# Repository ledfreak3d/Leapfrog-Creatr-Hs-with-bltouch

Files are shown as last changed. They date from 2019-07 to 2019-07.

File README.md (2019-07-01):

Latest Marlin firmware for Leapfrog Creatr Hs based on Marlin 2.0.0 Beta

100% Compatible with the original mainboard

### WARNING ! 	
These releases seems to break communication with the display (Olimex A20). 

( Probably because by defaut Creatr HS use Checksumed Protocol ? )
### WARNING ! 	

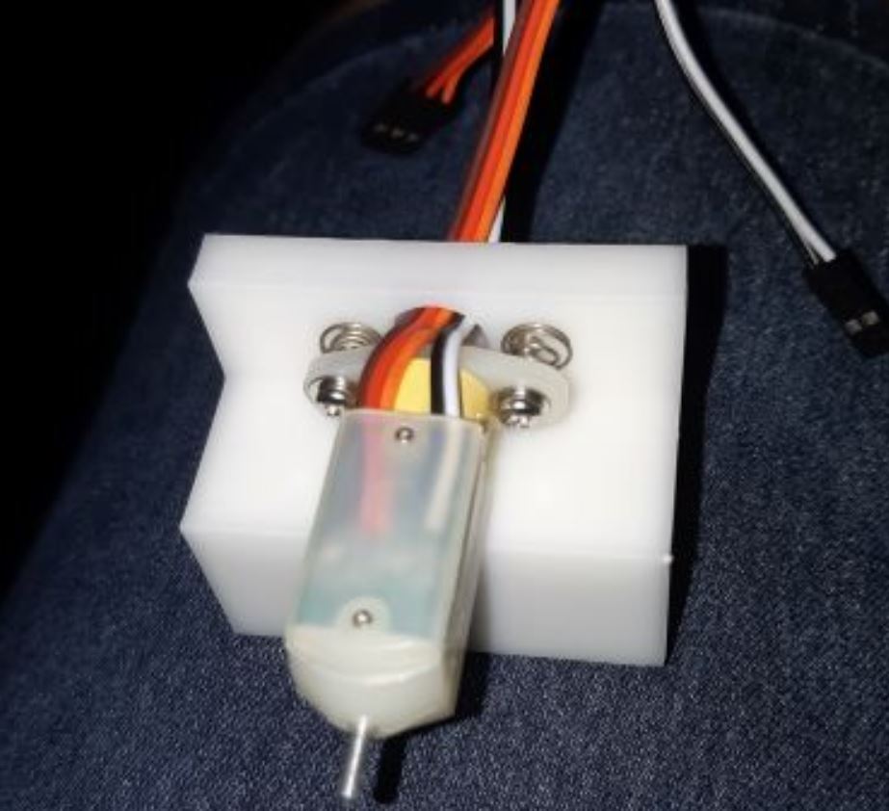
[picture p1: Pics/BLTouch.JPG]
BLTouch img


## Marlin BLTouch (same Standard settings)
- Add BLTouch
- Connect Z (Black/White) on Zmin connector
- Connect SERVO0_PIN on 52 (SCK) (physical pin 20 of ATMega2560) (see pictures)
 
Once installed, use this sequence to determine if the BLTouch is setup properly :

    Connect BLTouch, power up controller and upload the firmware
    
    LED will be ON if a servo signal is present.
    
    M119		; should return OPEN. If not check that the BLTouch is enabled in the configuration. If enabled then check wiring and Check that the correct pin is being used. Also check that Z_MIN_ENDSTOP_INVERTING and Z_MIN_PROBE_ENDSTOP_INVERTING are both set to "false".
    
    M280 P0 S10 	; should deploy the probe and the orange LED will be OFF.
    
    M119 		; should return OPEN
    
    M280 P0 S90 	; should stow the probe and the orange LED will be ON
    
    M280 P0 S60 	; puts it into the M119 test mode.
    		; The probe should remain stowed and the blue LED should be OFF. If it's ON then the unit needs to be adjusted.
    
    M119 		; should return TRIGGERED
    
    M280 P0 S160 	; returns it to normal operation
    
    M119 		; should return OPEN.
    
  After this Z offset needs to be callibrated !!!
  A good video guide to use for this is  https://www.youtube.com/watch?v=y_1Kg45APko&list=FLQG47LoNpPy0yjQeLG1prTA&index=2&t=0s
  
  Also make sure you setup your gcode correctly so auto bed leveling is done on every print
  See Simplify3d profiles for more info

Future update : 
 
-Upgrade to 32bit controller board

-Replacing the Olimex display for a touch display

-Upgrade Olimex to Octoprint

Cudo's to Vil Coyote for creating the mount that holds the bltouch
 
Forked from : https://github.com/CoyoteProd/Leapfrog-Creatr-HS/tree/master/Marlin%20BLTouch

Original Firmware : https://github.com/Leapfrog3DPrinters/CreatrHS_Firmware_2.5

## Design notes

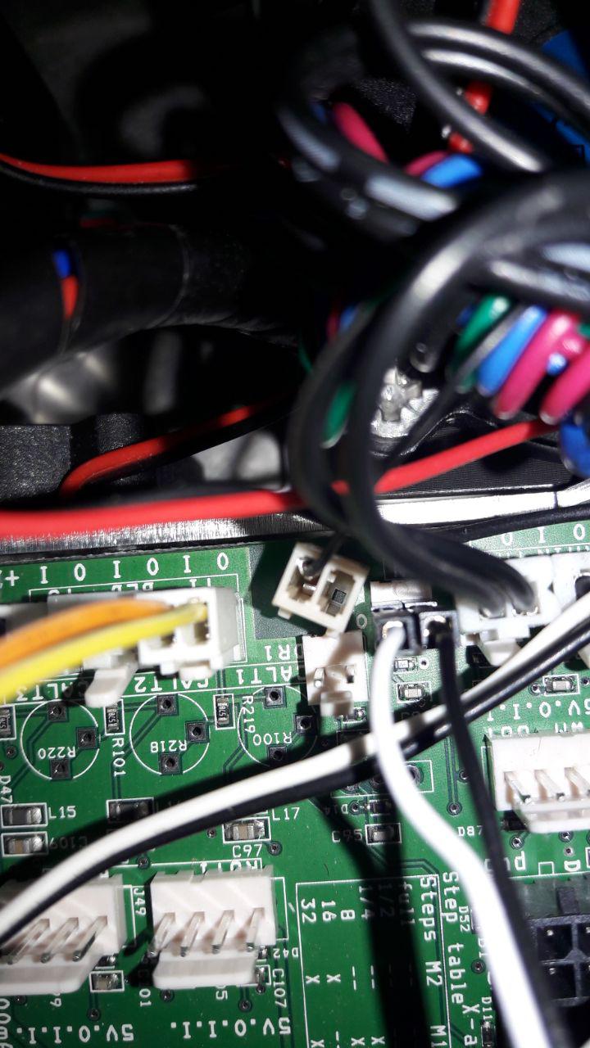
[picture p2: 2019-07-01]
Pics/Z-limit.jpg

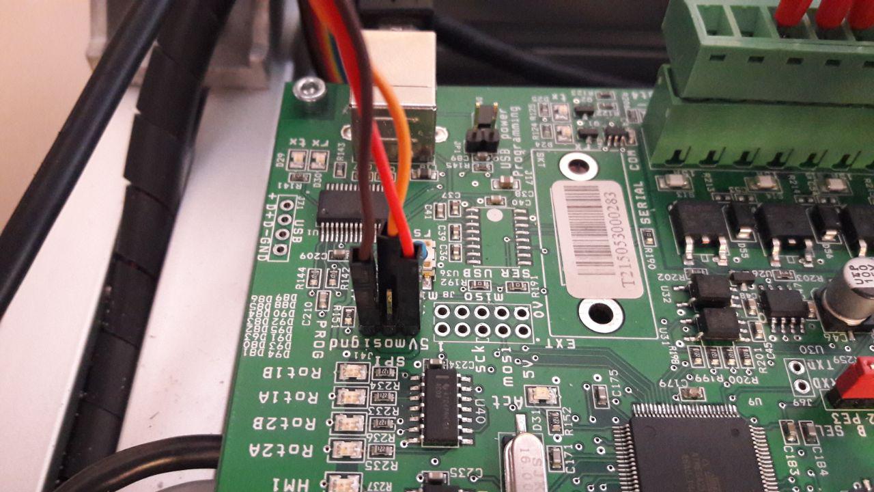
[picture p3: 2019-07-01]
Pics/Servo.jpg

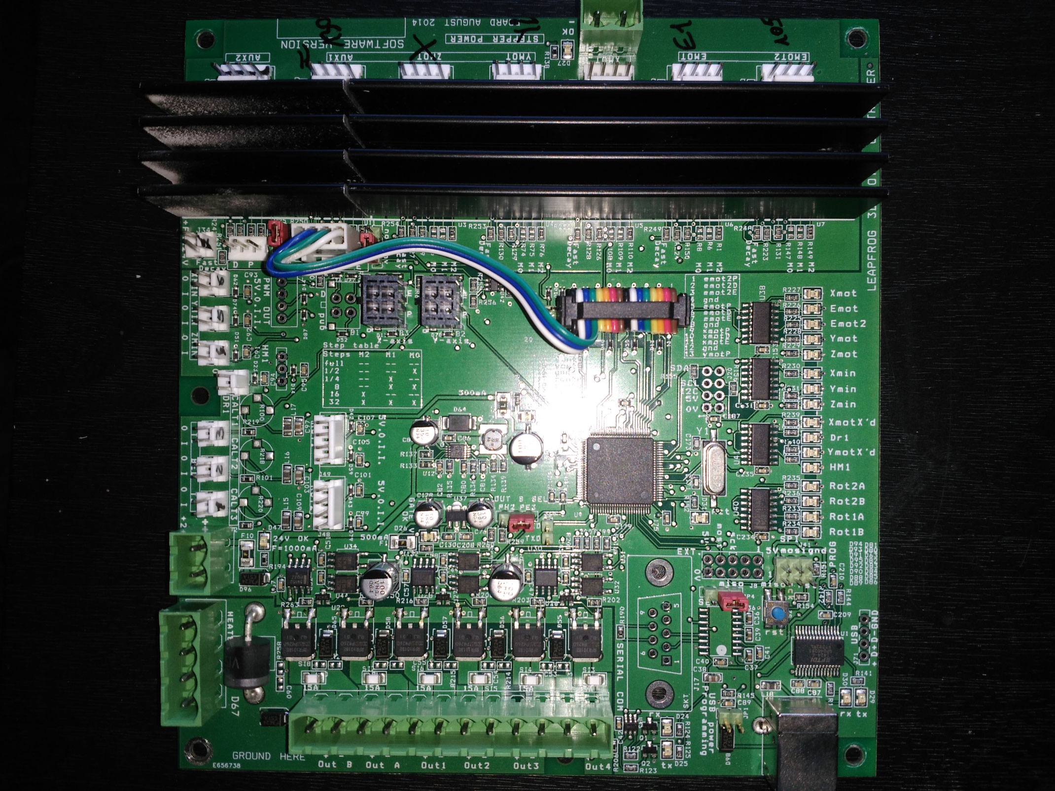
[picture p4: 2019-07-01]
Pics/image.jpg

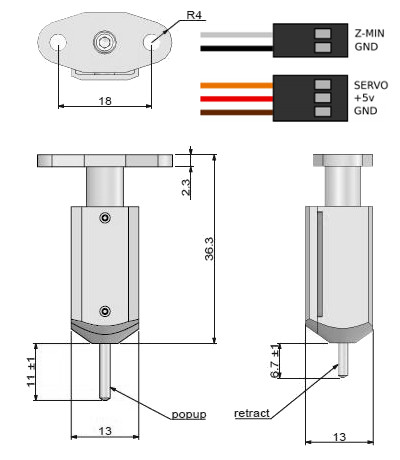
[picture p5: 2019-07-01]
Pics/BLTouch1.jpg

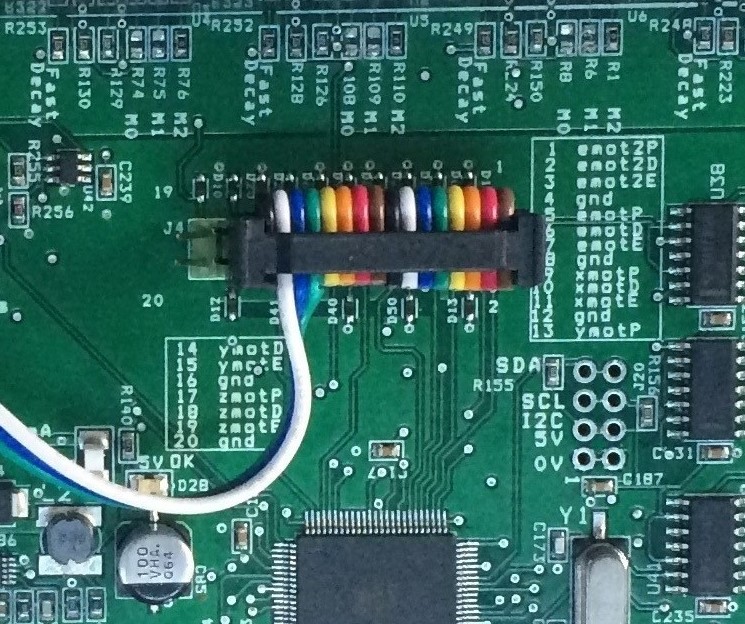
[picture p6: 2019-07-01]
Pics/oU3_eYAFjFmzLhcsRAwmdgnGUxJsZOXy3g (2).jpg

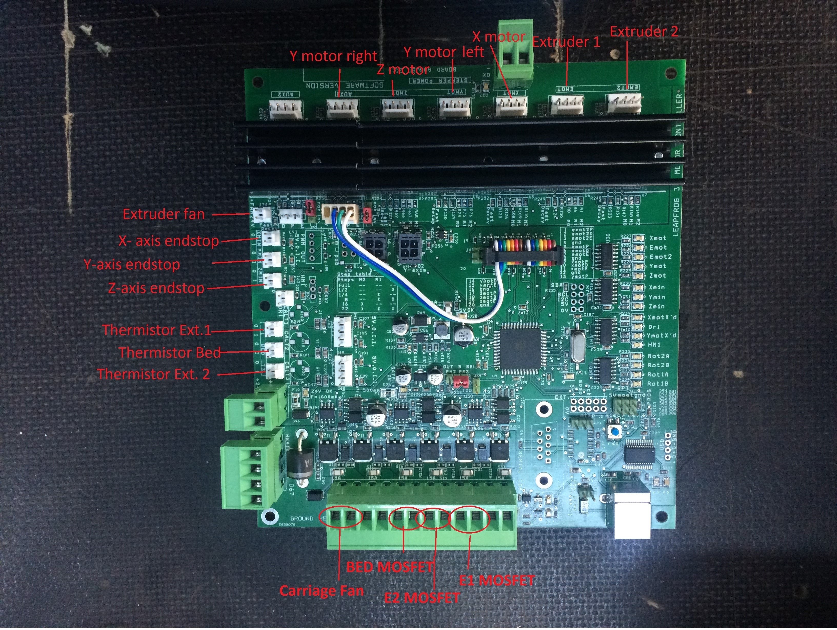
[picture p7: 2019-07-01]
Pics/oU3_eYAFjFmzLhcsRAwmdgnGUxJsZOXy3g.jpg

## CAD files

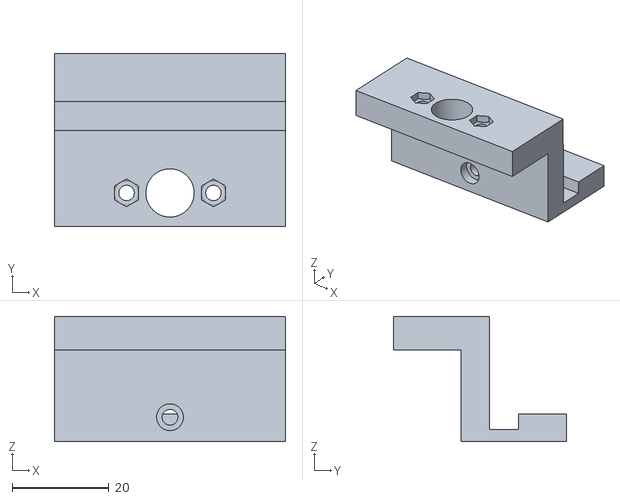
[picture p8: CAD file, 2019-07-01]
Support/support BLTouch.stl
47.9 x 35.9 x 26.0

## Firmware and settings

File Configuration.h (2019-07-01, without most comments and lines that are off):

#pragma once
#define CONFIGURATION_H_VERSION 020000
#define STRING_CONFIG_H_AUTHOR "(none, default config)" // Who made the changes.
#define SHOW_BOOTSCREEN
#define STRING_SPLASH_LINE1 SHORT_BUILD_VERSION // will be shown during bootup in line 1
#define STRING_SPLASH_LINE2 WEBSITE_URL         // will be shown during bootup in line 2
#define SERIAL_PORT 0
#define BAUDRATE 250000
  #define MOTHERBOARD BOARD_LEAPFROG
#define EXTRUDERS 2
#define DEFAULT_NOMINAL_FILAMENT_DIA 1.75
#define POWER_SUPPLY 0
#define TEMP_SENSOR_0 1
#define TEMP_SENSOR_1 1
#define TEMP_SENSOR_2 0
#define TEMP_SENSOR_3 0
#define TEMP_SENSOR_4 0
#define TEMP_SENSOR_5 0
#define TEMP_SENSOR_BED 1
#define TEMP_SENSOR_CHAMBER 0
#define DUMMY_THERMISTOR_998_VALUE 25
#define DUMMY_THERMISTOR_999_VALUE 100
#define MAX_REDUNDANT_TEMP_SENSOR_DIFF 10
#define TEMP_RESIDENCY_TIME     10  // (seconds) Time to wait for hotend to "settle" in M109
#define TEMP_WINDOW              1  // (°C) Temperature proximity for the "temperature reached" timer
#define TEMP_HYSTERESIS          3  // (°C) Temperature proximity considered "close enough" to the target
#define TEMP_BED_RESIDENCY_TIME 10  // (seconds) Time to wait for bed to "settle" in M190
#define TEMP_BED_WINDOW          1  // (°C) Temperature proximity for the "temperature reached" timer
#define TEMP_BED_HYSTERESIS      3  // (°C) Temperature proximity considered "close enough" to the target
#define HEATER_0_MINTEMP   5
#define HEATER_1_MINTEMP   5
#define HEATER_2_MINTEMP   5
#define HEATER_3_MINTEMP   5
#define HEATER_4_MINTEMP   5
#define HEATER_5_MINTEMP   5
#define BED_MINTEMP        5
#define HEATER_0_MAXTEMP 275
#define HEATER_1_MAXTEMP 275
#define HEATER_2_MAXTEMP 275
#define HEATER_3_MAXTEMP 275
#define HEATER_4_MAXTEMP 275
#define HEATER_5_MAXTEMP 275
#define BED_MAXTEMP      150
#define PIDTEMP
#define BANG_MAX 255     // Limits current to nozzle while in bang-bang mode; 255=full current
#define PID_MAX BANG_MAX // Limits current to nozzle while PID is active (see PID_FUNCTIONAL_RANGE below); 255=full current
#define PID_K1 0.95      // Smoothing factor within any PID loop
  #define PID_FUNCTIONAL_RANGE 20 // If the temperature difference between the target temperature and the actual temperature
#define  DEFAULT_Kp 11.07
#define  DEFAULT_Ki 0.44
#define  DEFAULT_Kd 71,39
#define MAX_BED_POWER 255 // limits duty cycle to bed; 255=full current
#define PREVENT_COLD_EXTRUSION
#define EXTRUDE_MINTEMP 170
#define PREVENT_LENGTHY_EXTRUDE
#define EXTRUDE_MAXLENGTH 200
#define THERMAL_PROTECTION_HOTENDS // Enable thermal protection for all extruders
#define THERMAL_PROTECTION_BED     // Enable thermal protection for the heated bed
#define THERMAL_PROTECTION_CHAMBER // Enable thermal protection for the heated chamber
#define USE_XMIN_PLUG
#define USE_YMIN_PLUG
#define USE_ZMIN_PLUG
#define ENDSTOPPULLUPS
#define X_MIN_ENDSTOP_INVERTING false // Set to true to invert the logic of the endstop.
#define Y_MIN_ENDSTOP_INVERTING false // Set to true to invert the logic of the endstop.
#define Z_MIN_ENDSTOP_INVERTING false // Set to true to invert the logic of the endstop.
#define X_MAX_ENDSTOP_INVERTING false // Set to true to invert the logic of the endstop.
#define Y_MAX_ENDSTOP_INVERTING false // Set to true to invert the logic of the endstop.
#define Z_MAX_ENDSTOP_INVERTING false // Set to true to invert the logic of the endstop.
#define Z_MIN_PROBE_ENDSTOP_INVERTING false // Set to true to invert the logic of the probe.
#define X_DRIVER_TYPE  DRV8825
#define Y_DRIVER_TYPE  DRV8825
#define Z_DRIVER_TYPE  DRV8825
#define E0_DRIVER_TYPE DRV8825
#define E1_DRIVER_TYPE DRV8825
#define DEFAULT_AXIS_STEPS_PER_UNIT   {(100.0/3)*2, (100.0/3)*2, 9600.0/10, 99.30}
#define DEFAULT_MAX_FEEDRATE          {300, 300, 30, 400}
#define DEFAULT_MAX_ACCELERATION      {3000,3000,100, 10000}
#define DEFAULT_ACCELERATION          3000    // X, Y, Z and E acceleration for printing moves
#define DEFAULT_RETRACT_ACCELERATION  3000    // E acceleration for retracts
#define DEFAULT_TRAVEL_ACCELERATION   3000    // X, Y, Z acceleration for travel (non printing) moves
  #define DEFAULT_XJERK 10.0
  #define DEFAULT_YJERK 10.0
  #define DEFAULT_ZJERK  0.4
#define DEFAULT_EJERK    5.0  // May be used by Linear Advance
#define Z_MIN_PROBE_USES_Z_MIN_ENDSTOP_PIN
#define BLTOUCH
#define X_PROBE_OFFSET_FROM_EXTRUDER 7  // X offset: -left  +right  [of the nozzle]
#define Y_PROBE_OFFSET_FROM_EXTRUDER -41  // Y offset: -front +behind [the nozzle]
#define Z_PROBE_OFFSET_FROM_EXTRUDER -1.71   // Z offset: -below +above  [the nozzle]
#define MIN_PROBE_EDGE 10
#define XY_PROBE_SPEED 8000
#define Z_PROBE_SPEED_FAST HOMING_FEEDRATE_Z
#define Z_PROBE_SPEED_SLOW (Z_PROBE_SPEED_FAST / 2)
#define Z_CLEARANCE_DEPLOY_PROBE   15 // Z Clearance for Deploy/Stow
#define Z_CLEARANCE_BETWEEN_PROBES  10 // Z Clearance between probe points
#define Z_CLEARANCE_MULTI_PROBE     5 // Z Clearance between multiple probes
#define Z_PROBE_LOW_POINT          -2 // Farthest distance below the trigger-point to go before stopping
#define Z_PROBE_OFFSET_RANGE_MIN -20
#define Z_PROBE_OFFSET_RANGE_MAX 20
#define X_ENABLE_ON 0
#define Y_ENABLE_ON 0
#define Z_ENABLE_ON 0
#define E_ENABLE_ON 0 // For all extruders
#define DISABLE_X false
#define DISABLE_Y false
#define DISABLE_Z false
#define DISABLE_E false             // For all extruders
#define DISABLE_INACTIVE_EXTRUDER   // Keep only the active extruder enabled
#define INVERT_X_DIR false
#define INVERT_Y_DIR false
#define INVERT_Z_DIR true
#define INVERT_E0_DIR false
#define INVERT_E1_DIR true
#define INVERT_E2_DIR false
#define INVERT_E3_DIR false
#define INVERT_E4_DIR false
#define INVERT_E5_DIR false
#define X_HOME_DIR -1
#define Y_HOME_DIR -1
#define Z_HOME_DIR -1
#define X_BED_SIZE 270
#define Y_BED_SIZE 280
#define X_MIN_POS 0
#define Y_MIN_POS 0
#define Z_MIN_POS 0
#define X_MAX_POS X_BED_SIZE
#define Y_MAX_POS Y_BED_SIZE
#define Z_MAX_POS 180
#define MIN_SOFTWARE_ENDSTOPS
  #define MIN_SOFTWARE_ENDSTOP_X
  #define MIN_SOFTWARE_ENDSTOP_Y
  #define MIN_SOFTWARE_ENDSTOP_Z
#define MAX_SOFTWARE_ENDSTOPS
  #define MAX_SOFTWARE_ENDSTOP_X
  #define MAX_SOFTWARE_ENDSTOP_Y
  #define MAX_SOFTWARE_ENDSTOP_Z
#define AUTO_BED_LEVELING_BILINEAR
  #define ENABLE_LEVELING_FADE_HEIGHT
  #define SEGMENT_LEVELED_MOVES
  #define LEVELED_SEGMENT_LENGTH 5.0 // (mm) Length of all segments (except the last one)
  #define GRID_MAX_POINTS_X 3
  #define GRID_MAX_POINTS_Y GRID_MAX_POINTS_X
#define Z_SAFE_HOMING
  #define Z_SAFE_HOMING_X_POINT ((X_BED_SIZE) / 2)    // X point for Z homing when homing all axes (G28).
  #define Z_SAFE_HOMING_Y_POINT ((Y_BED_SIZE) / 2)    // Y point for Z homing when homing all axes (G28).
#define HOMING_FEEDRATE_XY (50*60)
#define HOMING_FEEDRATE_Z  (4*60)
#define VALIDATE_HOMING_ENDSTOPS
#define EEPROM_SETTINGS     // Persistent storage with M500 and M501
#define EEPROM_CHITCHAT       // Give feedback on EEPROM commands. Disable to save PROGMEM.
#define HOST_KEEPALIVE_FEATURE        // Disable this if your host doesn't like keepalive messages
#define DEFAULT_KEEPALIVE_INTERVAL 2  // Number of seconds between "busy" messages. Set with M113.
#define BUSY_WHILE_HEATING            // Some hosts require "busy" messages even during heating
#define PREHEAT_1_LABEL       "PLA"
#define PREHEAT_1_TEMP_HOTEND 180
#define PREHEAT_1_TEMP_BED     70
#define PREHEAT_1_FAN_SPEED     0 // Value from 0 to 255
#define PREHEAT_2_LABEL       "ABS"
#define PREHEAT_2_TEMP_HOTEND 240
#define PREHEAT_2_TEMP_BED    110
#define PREHEAT_2_FAN_SPEED     0 // Value from 0 to 255
#define PRINTJOB_TIMER_AUTOSTART
#define LCD_LANGUAGE en
#define DISPLAY_CHARSET_HD44780 JAPANESE
#define LCD_INFO_SCREEN_STYLE 0
#define SOFT_PWM_SCALE 0
#define SERVO_DELAY { 300 }

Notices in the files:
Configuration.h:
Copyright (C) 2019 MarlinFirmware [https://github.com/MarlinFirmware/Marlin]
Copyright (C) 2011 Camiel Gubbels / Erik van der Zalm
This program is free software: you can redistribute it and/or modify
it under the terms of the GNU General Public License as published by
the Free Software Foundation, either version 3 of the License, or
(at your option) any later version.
